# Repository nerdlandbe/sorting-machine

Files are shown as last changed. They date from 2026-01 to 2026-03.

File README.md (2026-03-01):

# M&M sorteermachine

Deze sorteermachine is met 3D-geprinte onderdelen en een aantal elektronica componenten te maken.

Het bovenste gedeelte is gebaseerd op [deze sorteermachine](https://www.instructables.com/Arduino-MM-Color-Sorter/). Het onderste gedeelte is bijgemaakt en de code is helemaal herschreven.

Met deze verbetering zie je alles nog beter en is de code ook duidelijker.

## Materiaal

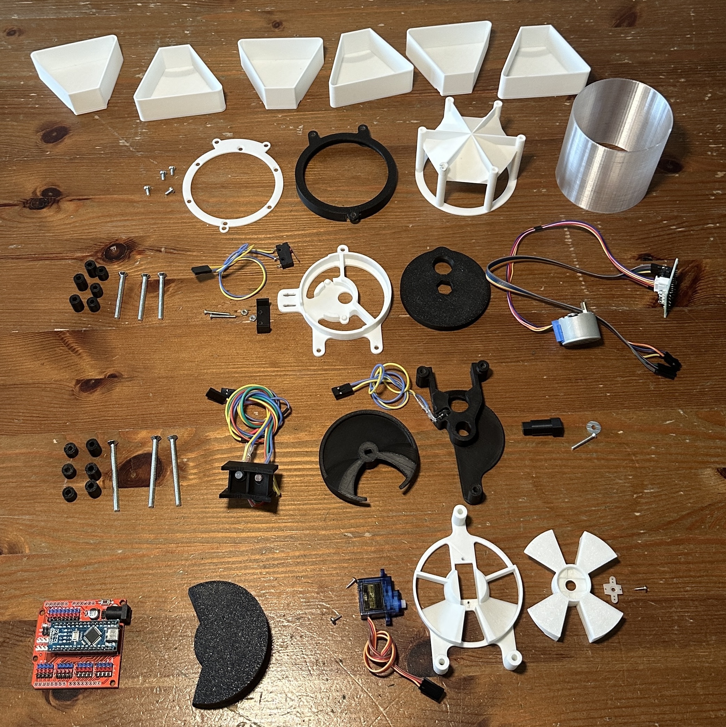
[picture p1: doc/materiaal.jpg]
Materiaal


### Te 3D-printen onderdelen

- [center_pin.stl](3D-files/center_pin.stl)
- [central_compartment.stl](3D-files/central_compartment.stl)
- [container.stl](3D-files/container.stl)
- [final_divider.stl](3D-files/final_divider.stl)
- [funnel_cap.stl](3D-files/funnel_cap.stl)
- [lid.stl](3D-files/lid.stl)
- [limit_switch_holder.stl](3D-files/limit_switch_holder.stl)
- [lower_disk.stl](3D-files/lower_disk.stl)
- [recipient.stl](3D-files/recipient.stl) (6 keer)
- [secondary_funnel.stl](3D-files/secondary_funnel.stl)
- [sensor_housing.stl](3D-files/sensor_housing.stl)
- [sorter-base.stl](3D-files/sorter-base.stl)
- [sorter-topring.stl](3D-files/sorter-topring.stl)
- [top_layer.stl](3D-files/top_layer.stl)
- [upper_disk.stl](3D-files/upper_disk.stl)
- [washer-08mm.stl](3D-files/washer-08mm.stl) (3 keer)
- [washer-10mm.stl](3D-files/washer-10mm.stl) (3 keer)
- [washer-14mm.stl](3D-files/washer-14mm.stl) (6 keer)

Je kan de kleur van alle onderdelen kiezen zoals je zelf wil, alleen [sensor_housing.stl](3D-files/sensor_housing.stl) en  [central_compartment.stl](3D-files/central_compartment.stl) moeten in het zwart om de kleurselectie te laten werken.

### Electronica componenten

- Arduino uno of nano
- Breadboard of nano expansion board
- LDR (lichtsensor)
- RGB led 5mm
- Witte led 5mm
- Weerstand 220 ohm (4 keer)
- Weerstand 10k ohm
- Microswitch [SS-5GL](https://www.amazon.com.be/s?k=micro+switch+SS-5GL)
- Servo motor [Microservo 9G + accessoires](https://www.amazon.com.be/Micro-9g-Servo/s?k=Micro+9g+Servo)
- Stepper motor [5V 28BYJ-48 met ULN2003 drivershield](https://www.amazon.com.be/s?k=stepper+28BYJ-48+ULN2003)
- Dupont breadboardkabels
- Montagekabels

### Montage

- Bout M4 X 50 (3 stuks)
- Bout M4 X 40 (3 stuks)
- Bout M3 x 5 of M3 x 8 (4 stuks)
- Bout M2.5 x 20 (3 stuks)
- Moer M2.5 (2 stuks)
- Rondel M2.5 (1 stuk)
- Vijsjes die bij de servokit zitten

### Code

Laad deze repo in Visual Studio Code, pas mogelijks [platformio.ini](platformio.ini) aan om de juiste arduino te selecteren en laad de code op.

Alle code staat in [main.cpp](src/main.cpp) mocht je de Arduino IDE gebruiken.

## Electronicaschema

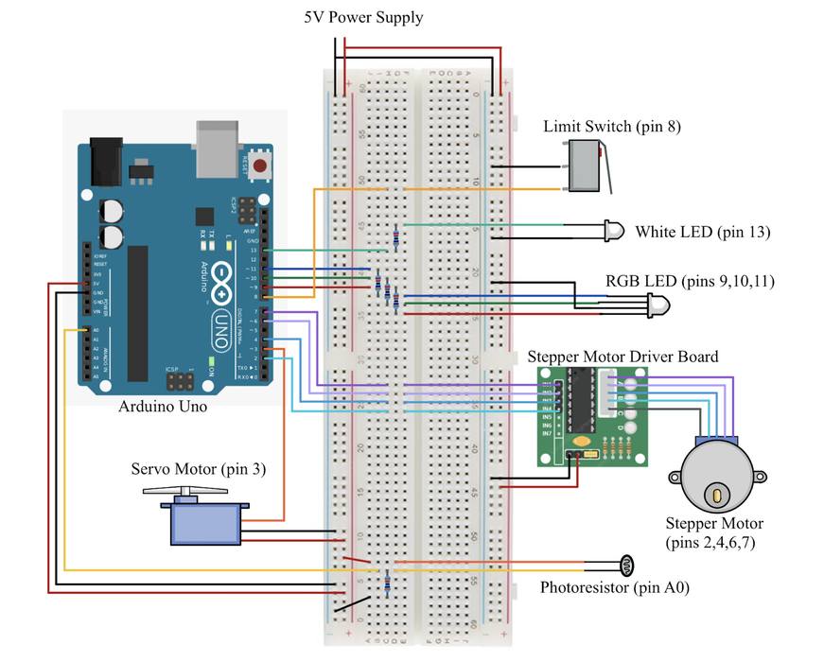
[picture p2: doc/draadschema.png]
draadschema


Ofwel gebruik je arduino (uno of nano) en een breadboard, ofwel een arduino nano met [expansion board](https://www.amazon.com.be/s?k=arduino+nano+expansion+board) (zoals bij de opnames).

## Montage bovenste gedeelte

Het bovenste gedeelte is gebaseerd op de [M&M sorter](https://www.instructables.com/Arduino-MM-Color-Sorter/) van Jackofalltrades_.

Als het onduidelijk is hoe de onderdelen tegen elkaar moeten geplaatst worden, dit is het schema van de onderdelen van het bovenste gedeelte:

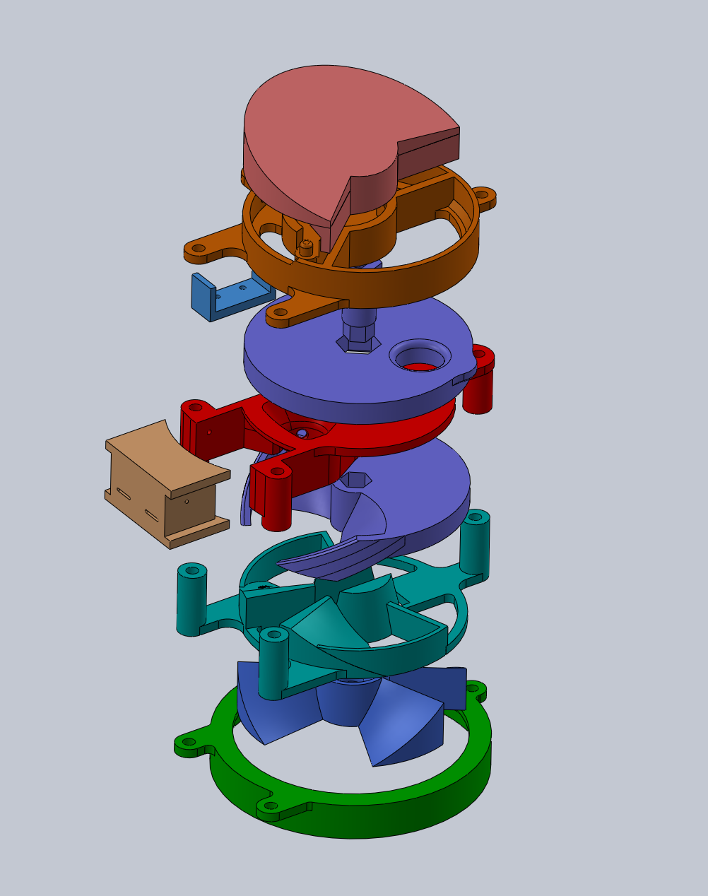
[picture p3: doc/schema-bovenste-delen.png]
bovenste delen


### Servo + behuizing onderste sorteerder

Bij de servo zitten vijsjes en ook een wit kruis dat je op de servo kan vijzen. Je moet dit een beetje bijknippen zoals op de foto's hieronder. Op die manier past het in de 3D-print.

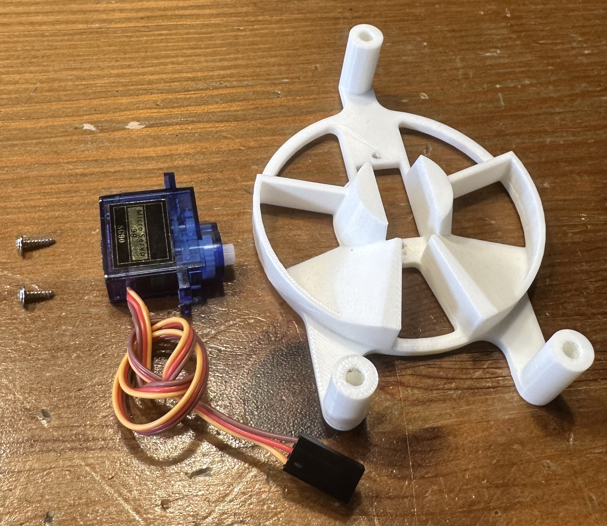
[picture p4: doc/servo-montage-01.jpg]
Servo stap 1

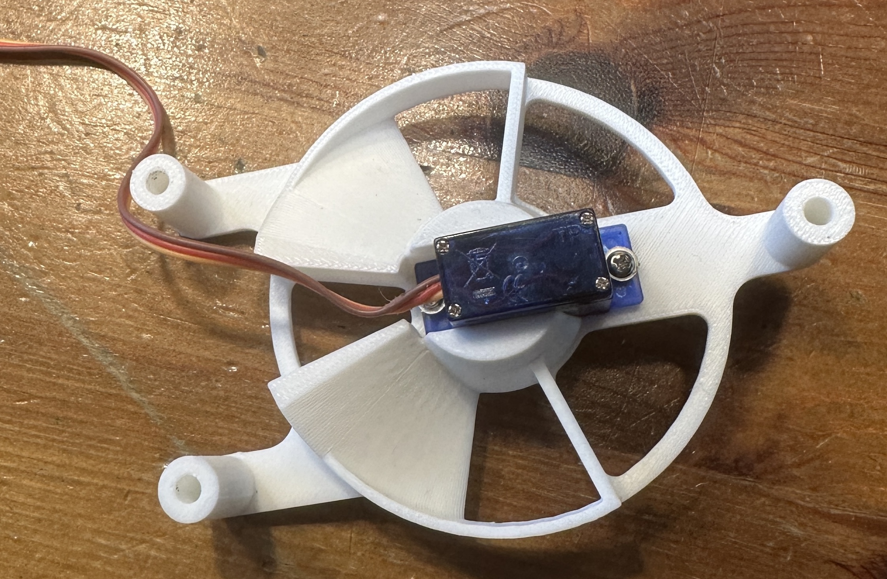
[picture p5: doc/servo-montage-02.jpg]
Servo stap 2

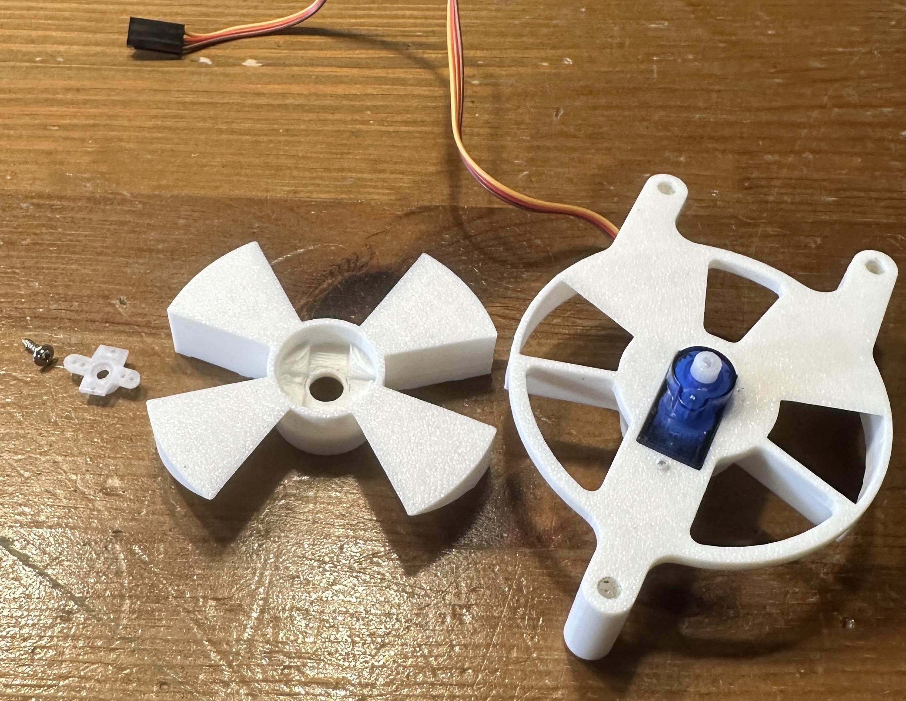
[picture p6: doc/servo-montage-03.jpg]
Servo stap 3

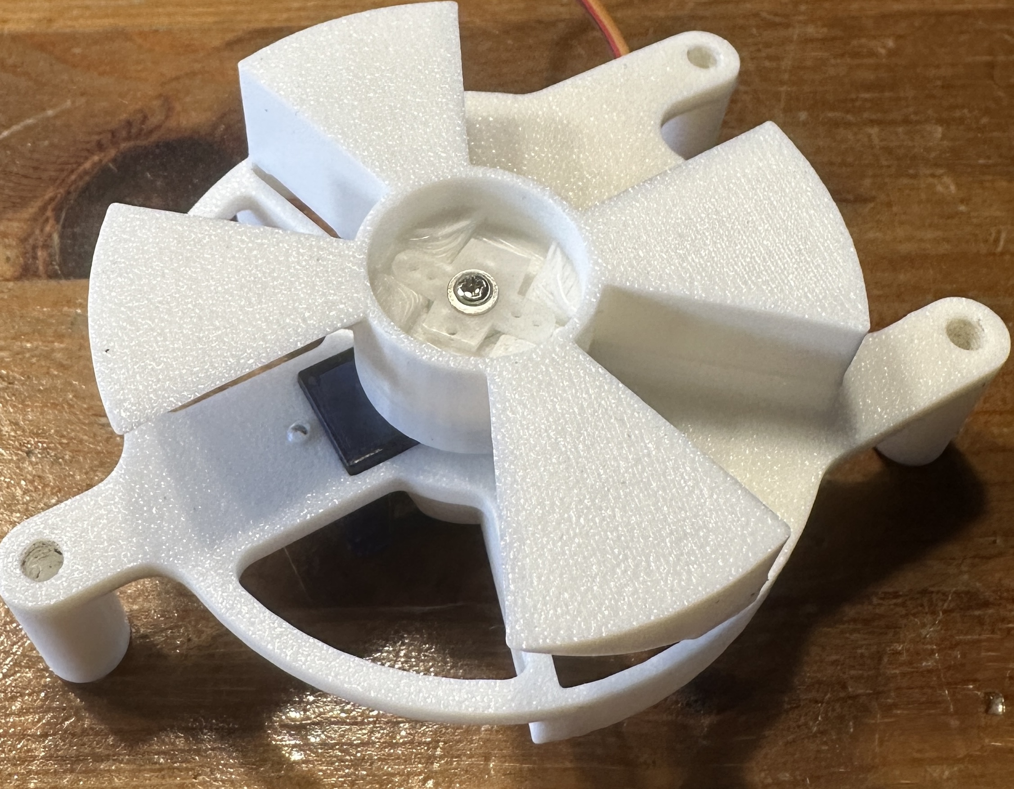
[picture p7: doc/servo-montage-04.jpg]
Servo stap 4


### Witte led behuizing

Gebruik een 220 Ohm weerstand voor de witte led.
Soldeer draadjes aan de led om de led en de weerstand te kunnen verbinden.
Lijm de led daarna vast in de 3D-print.

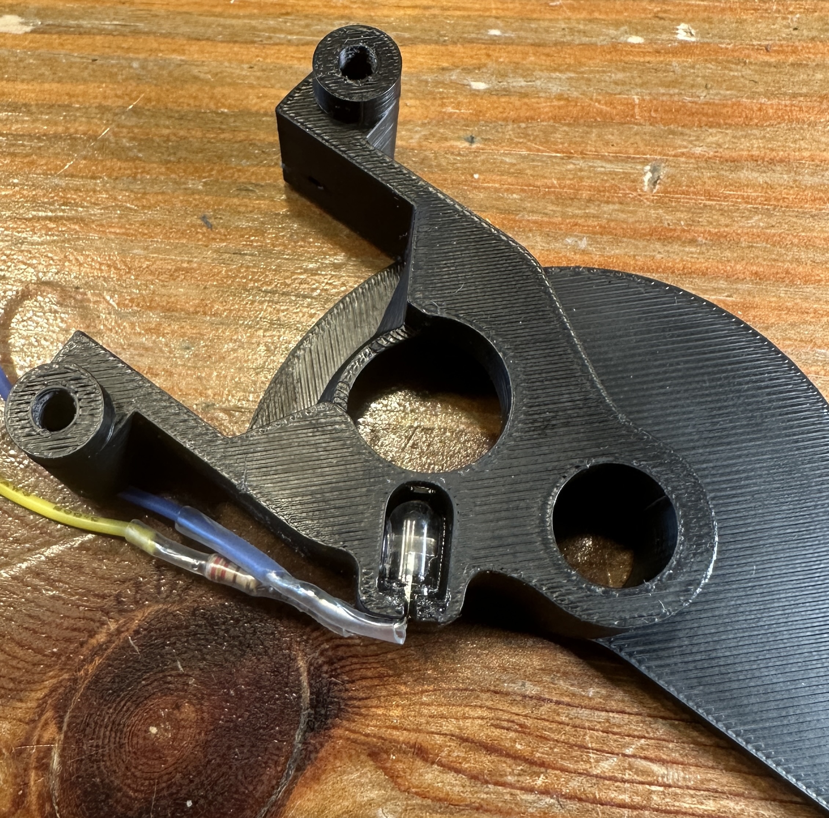
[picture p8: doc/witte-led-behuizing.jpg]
Witte led behuizing


### Bovenste sorteerder

Gebruik een M2.5 x 20 bout en rondel

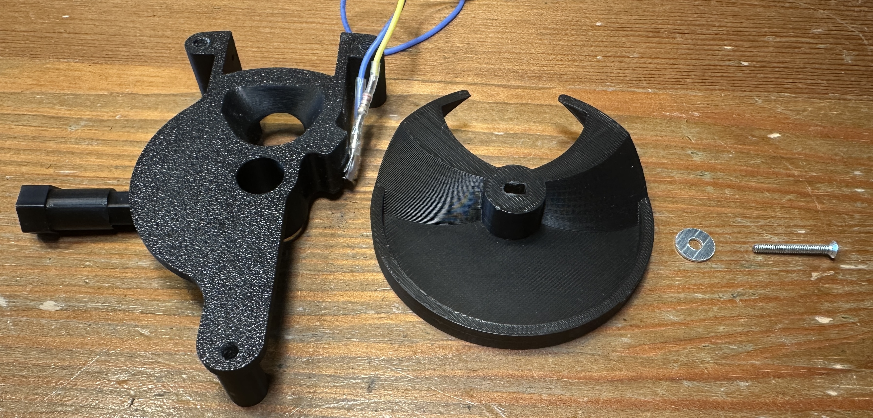
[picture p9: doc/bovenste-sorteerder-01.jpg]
bovenste sorteerder 01

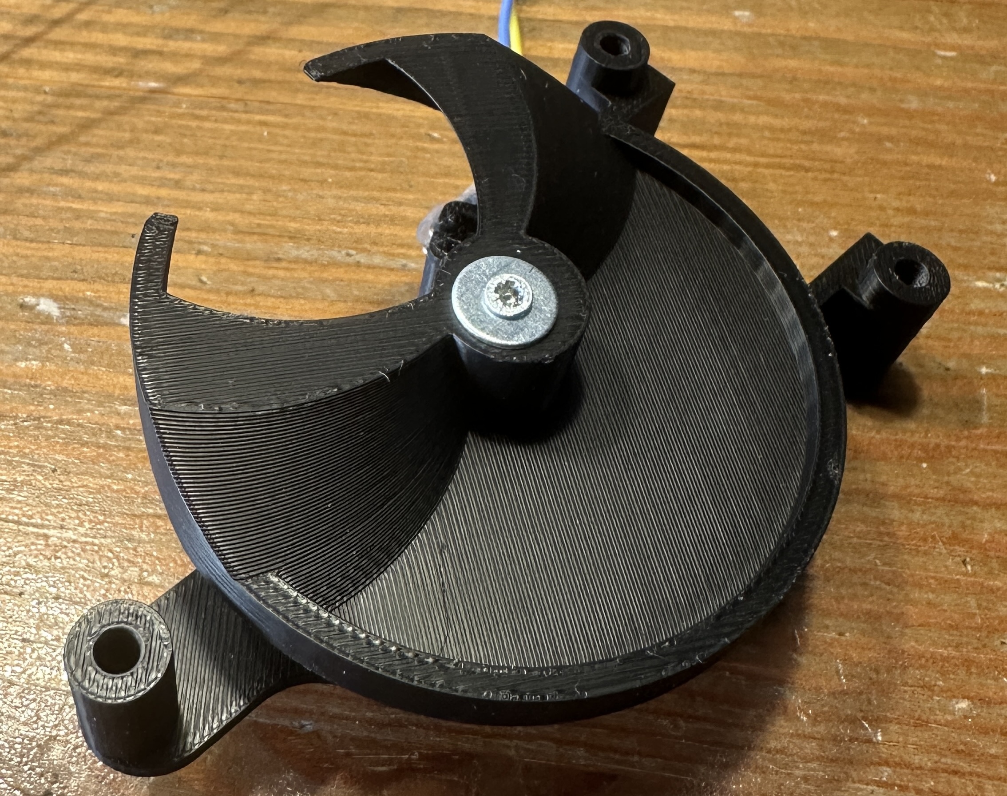
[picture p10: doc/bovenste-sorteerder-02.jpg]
bovenste sorteerder 02

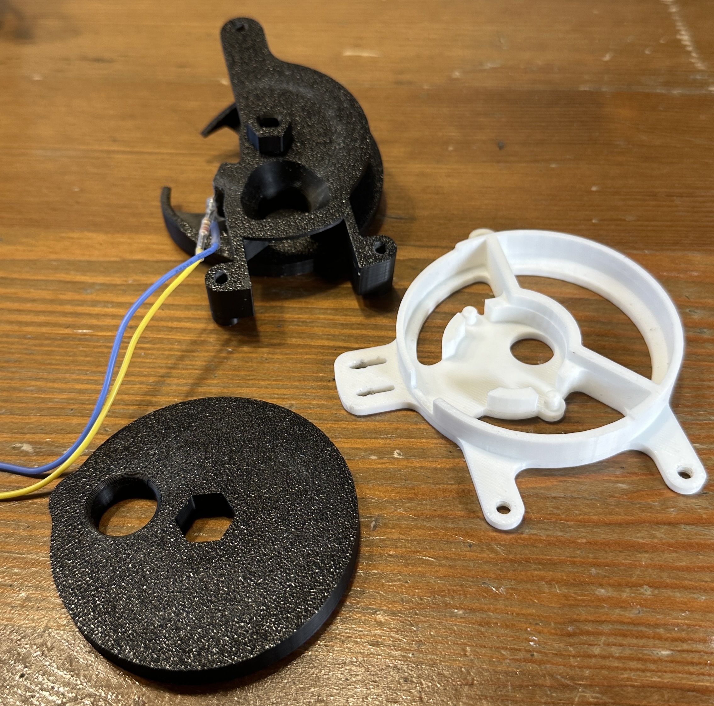
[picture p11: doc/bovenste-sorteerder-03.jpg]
bovenste sorteerder 03


### Bovenste en onderste sorteerder samen

Gebruik drie M4 X 50 bouten, drie 8mm washers en drie 14mm washers.

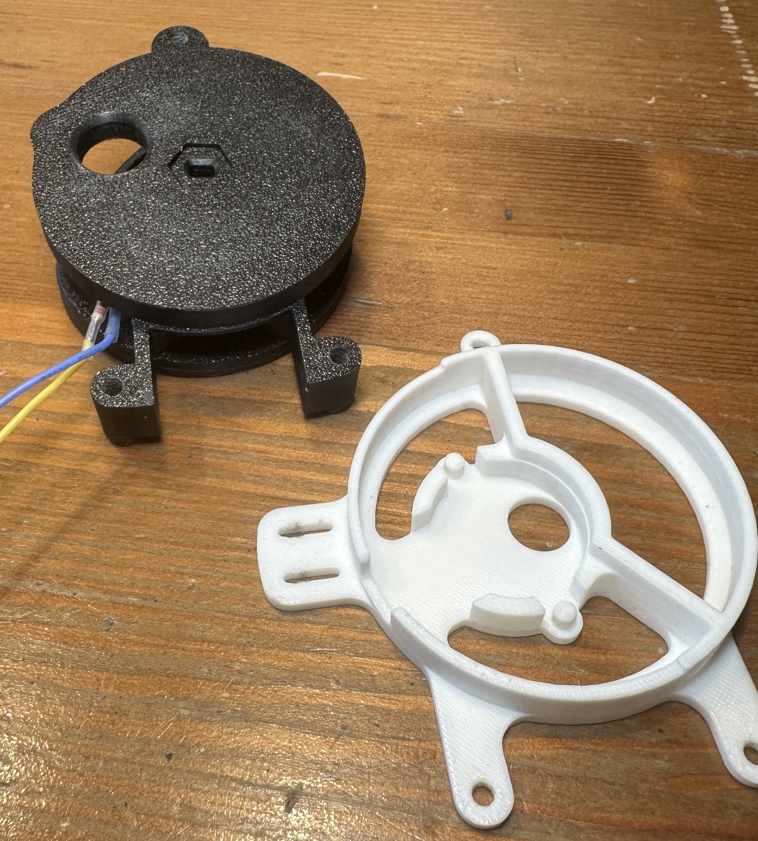
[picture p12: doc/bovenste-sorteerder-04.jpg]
bovenste sorteerder 04

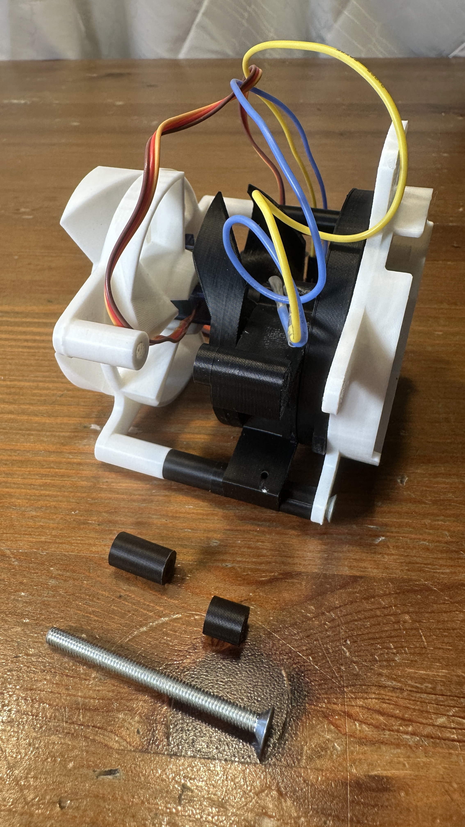
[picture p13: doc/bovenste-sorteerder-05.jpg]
bovenste sorteerder 05

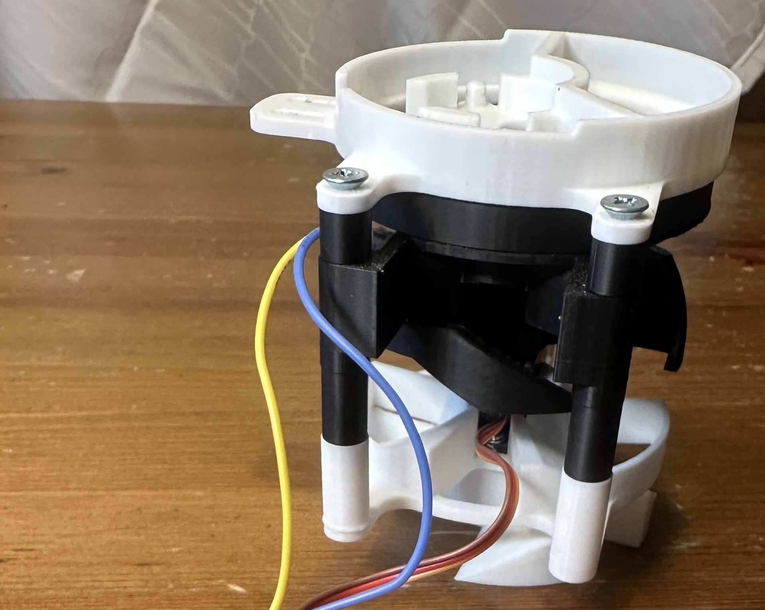
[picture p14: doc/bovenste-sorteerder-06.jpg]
Montage klaar van bovenste en onderste sorteerder


### Controlekamer

De controlekamer bestond al uit de witte LED uit een vorige stap. Met dit extra onderdeel maak je de controlekamer helemaal licht dicht.

Bevestig de RGBled (zorg dat de pin van iedere kleur een weerstand van 220 Ohm heeft) en de licht sensor (LDR sensor met zijn schakeling, zie [het draadschema](doc/draadschema.png) hiervoor).

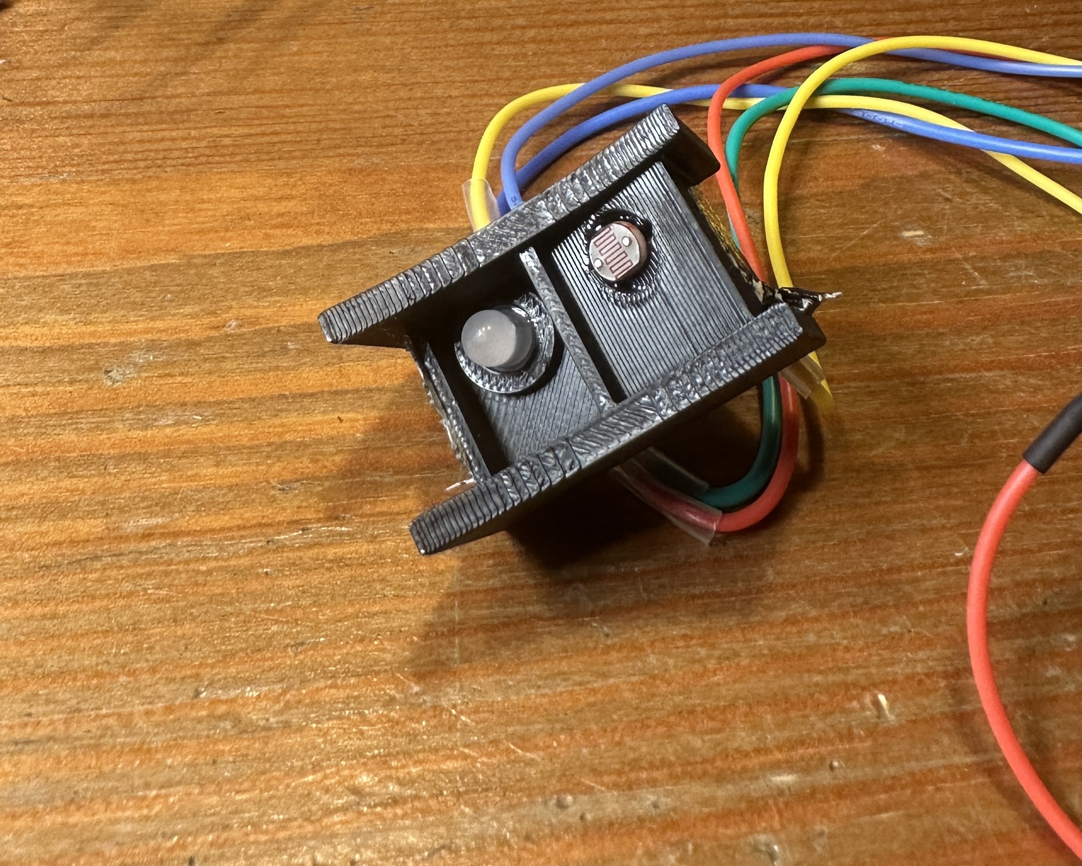
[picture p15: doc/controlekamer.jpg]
Controlekamer


Duw de gemonteerde controle zachtjes op zijn plaats. Hij moet stevig vastzitten en geen licht van buitenaf doorlaten.

Mogelijks helpt het om wat extra plakband aan te brengen zodat hij goed vast zit.

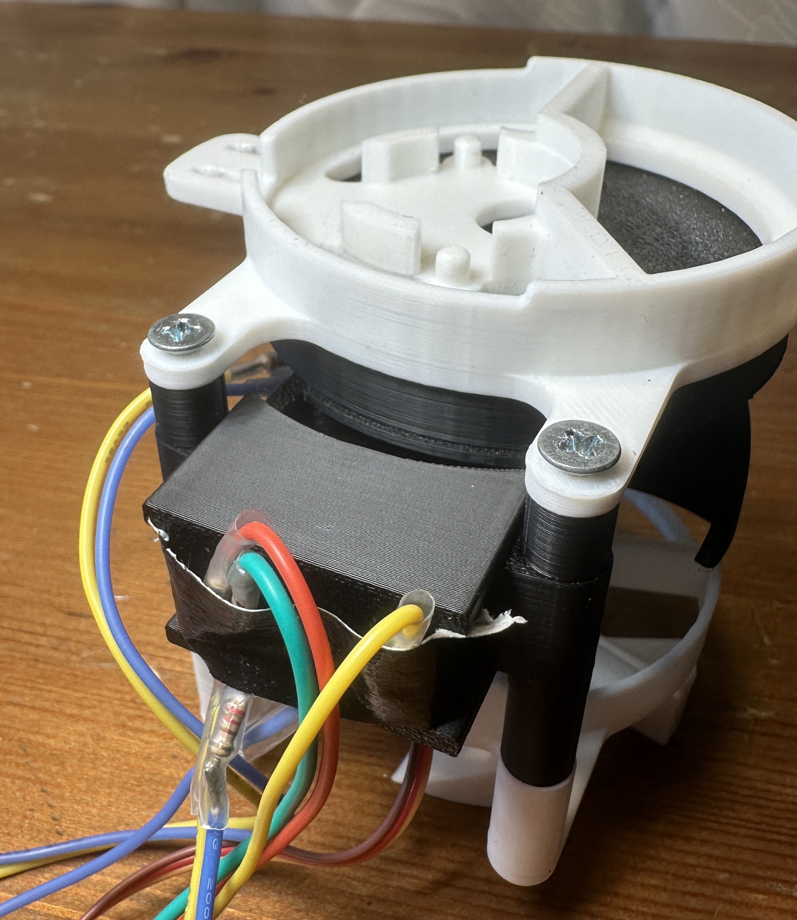
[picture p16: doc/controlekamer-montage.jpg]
montage controlekamer

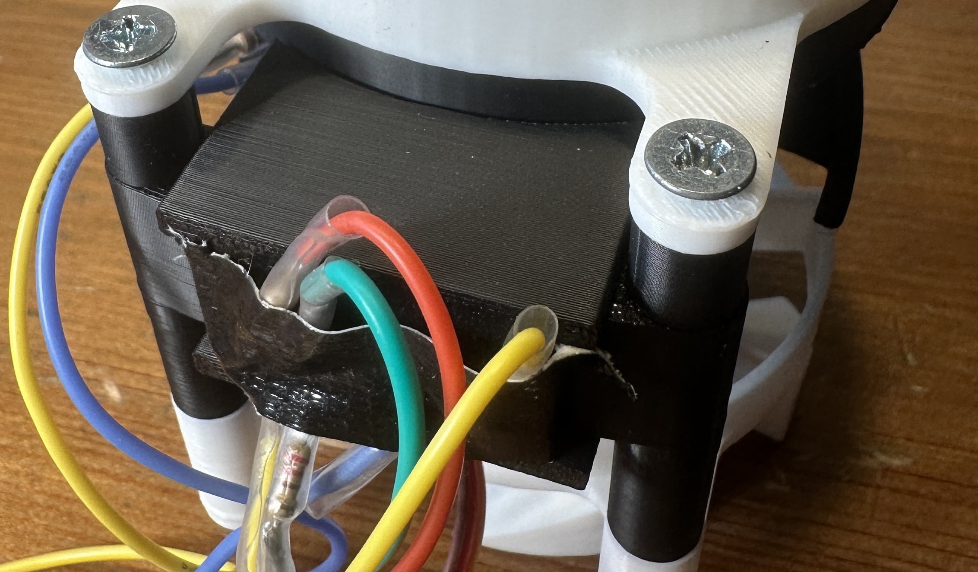
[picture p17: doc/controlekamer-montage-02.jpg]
controlekamer gemonteerd


### Microswitch

Gebruik twee M2.5 X 20 bouten en moeren.

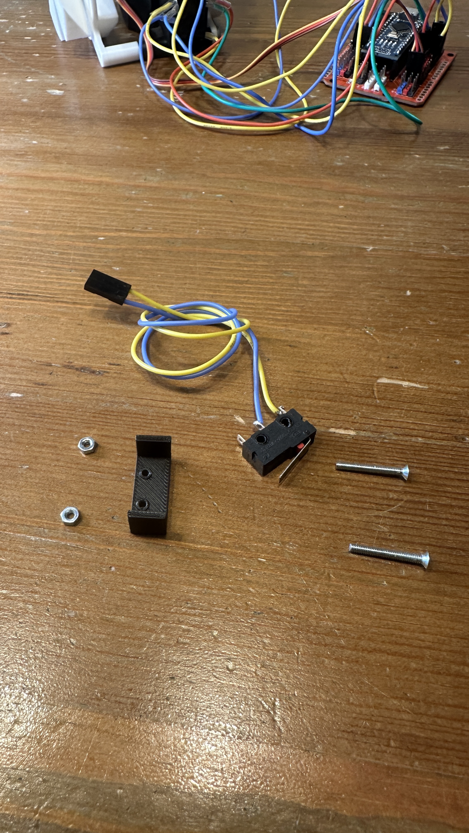
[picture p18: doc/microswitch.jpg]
Microswitch


De microswitch geeft een signaal wanneer de bovenste sorteerder een M&M in de controlekamer heeft gelegd.

Deze stap heeft wat extra mechanische configuratie nodig. De microswitch moet namelijk ingedrukt zijn (je hoort een klikje) als de verdikking van de zwarte schijf met gat voorbij de microswitch passeert.

De twee vijsjes moeten mogelijks een beetje in de gleuven van het witte onderdeel naar voor of achter geschoven worden.

Let ook op de orientatie van de microswitch. De kleuren van de draadjes op de foto kan je gebruiken om de open beugel van de microswitch in de juiste richting te monteren.

Als je de schijf een paar keer hebt kunnen ronddraaien en iedere keer een klik gehoord hebt én de schijf vlotjes is kunnen verder draaien, draai dan de vijsjes en de bouten goed vast aan.

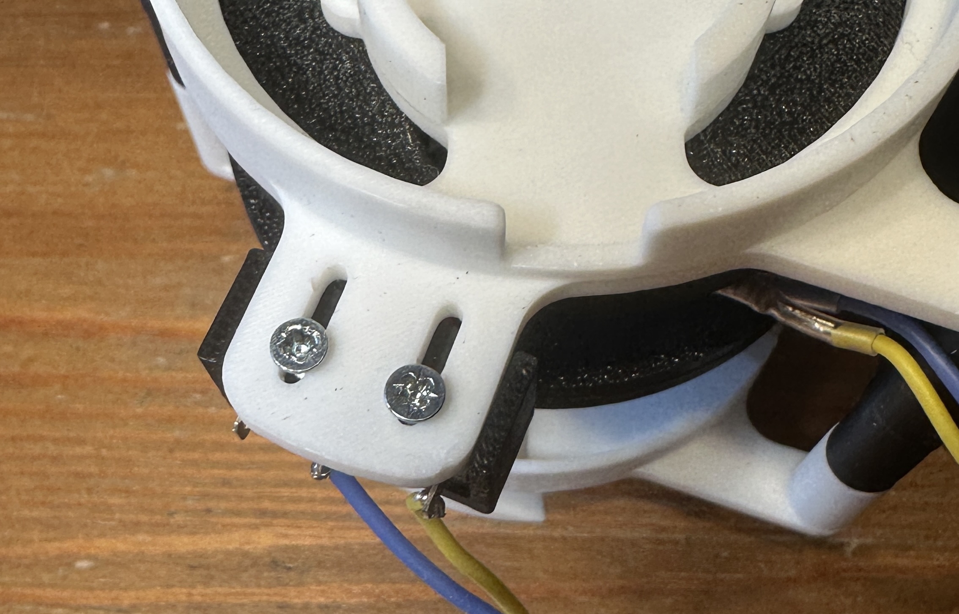
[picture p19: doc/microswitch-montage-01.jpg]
Microswitch nontage

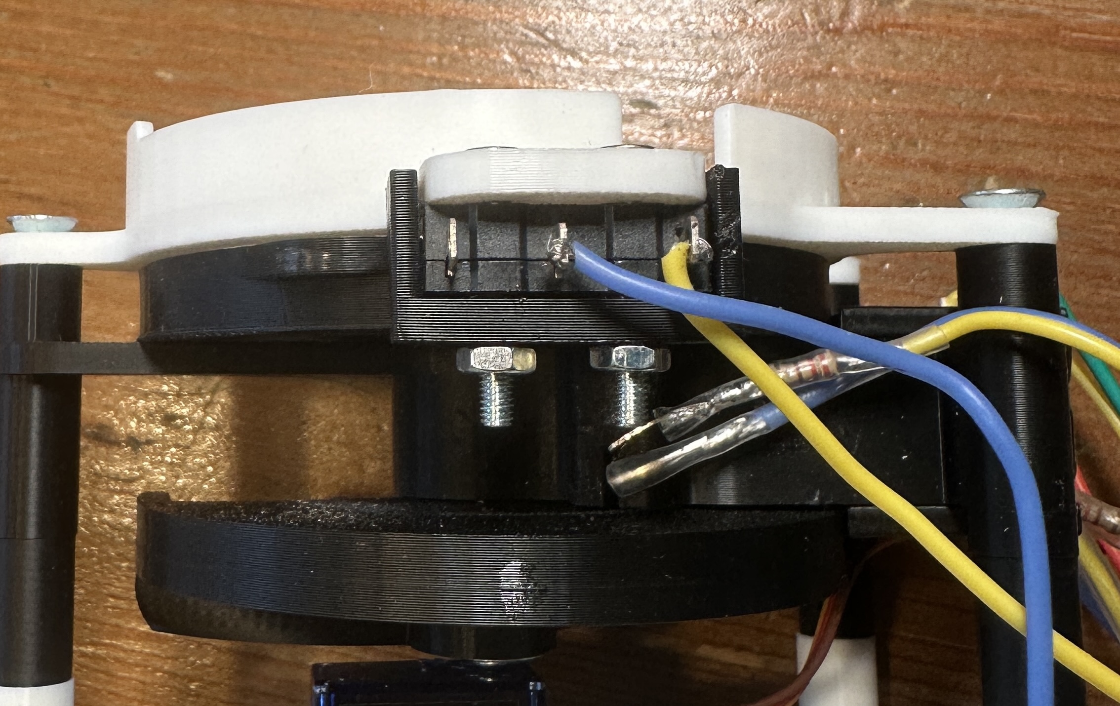
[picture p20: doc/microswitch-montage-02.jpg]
Microswitch nontage


### Steppermotor

Neem de steppermotor en je zal een rechthoekige sleuf zien. Steek de steppermotor in de witte behuizing (hij blijft normaal gezien vast zitten van zichzelf) en draai aan de zwarte schijf tot de pin van de servo mooi in de gleuf past.

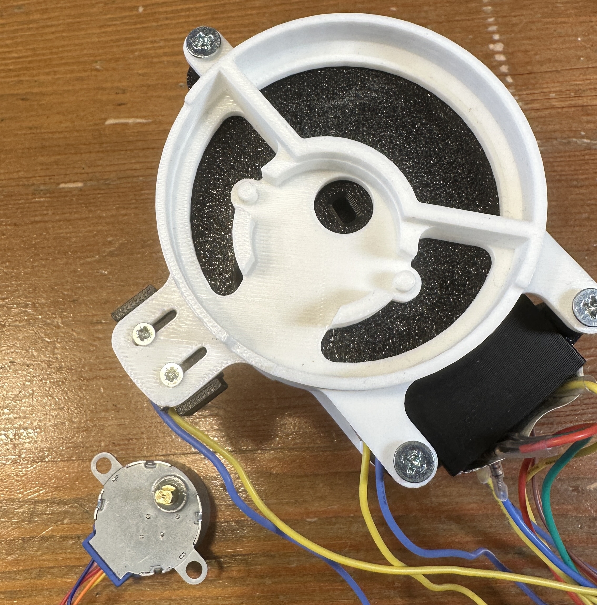
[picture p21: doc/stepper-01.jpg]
Stepper 01

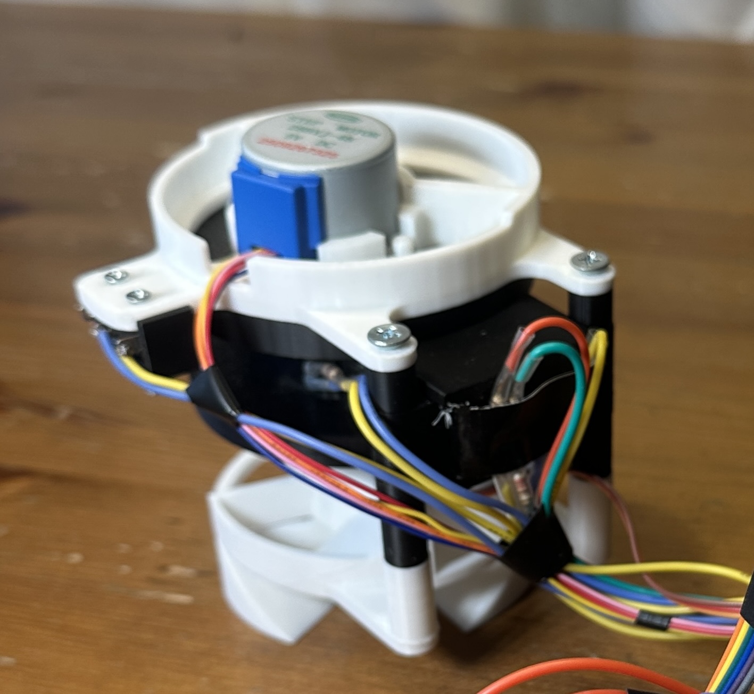
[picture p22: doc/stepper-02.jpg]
Stepper 02


### Afwerking bovenste deel

Neem wat plakband om de draadjes mooi samen te binden zodat die niet vast komen te zitten in het mechanisme.

Het bovenste deel is nu compleet!

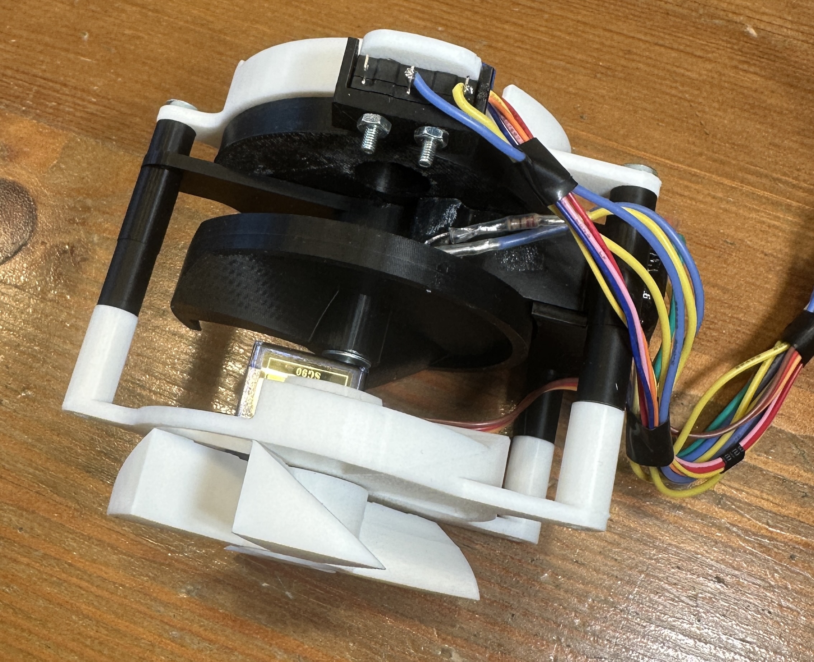
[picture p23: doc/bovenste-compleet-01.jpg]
Bovenste deel 01

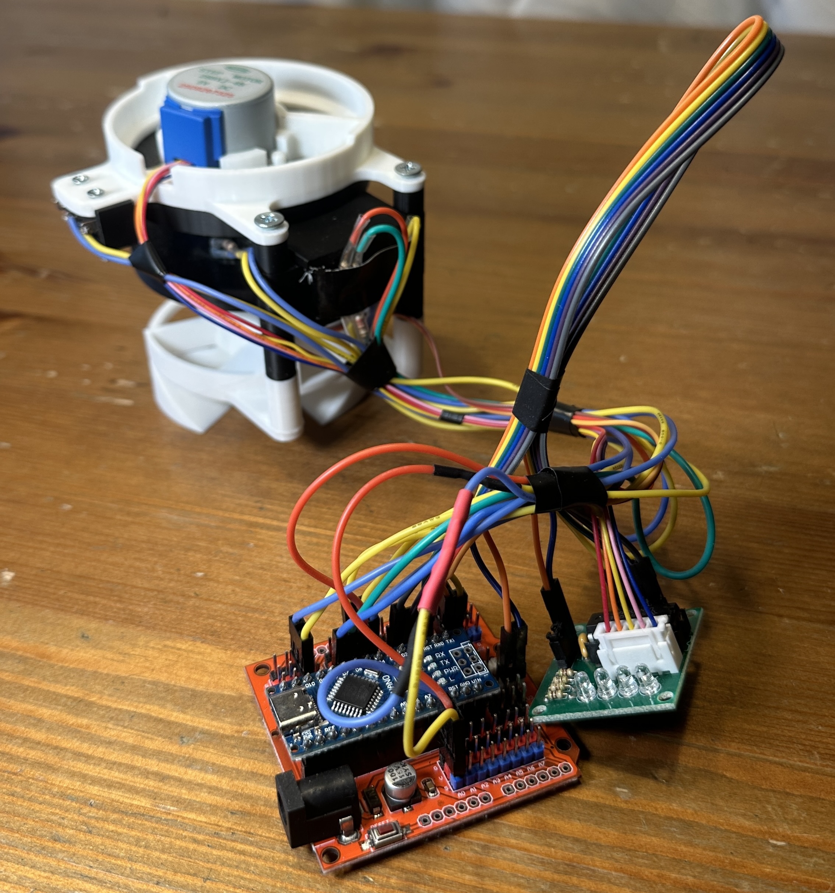
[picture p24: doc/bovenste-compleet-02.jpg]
Bovenste deel 02


## Servocalibratie

Het kan zijn dat je de onderste sorteerschijf anders gemonteerd hebt.

De onderste schijf moet op drie posities komen te staan. Om dit te testen, zoek deze lijn code en wis de twee ``//`` voor ``#define``

```
// Uncomment to do servo position testing only
//#define doServoTest true
```

Upload de code nu en de machine zal heel de tijd deze drie posities aflopen.

**Let wel op!** De machine is nog niet compleet. Hou  hem vast of zet hem ondersteboven zodat hij niet omvalt of kapot gaat. 

Kijk visueel of de posities overenkomen met de posities op de foto's hieronder.

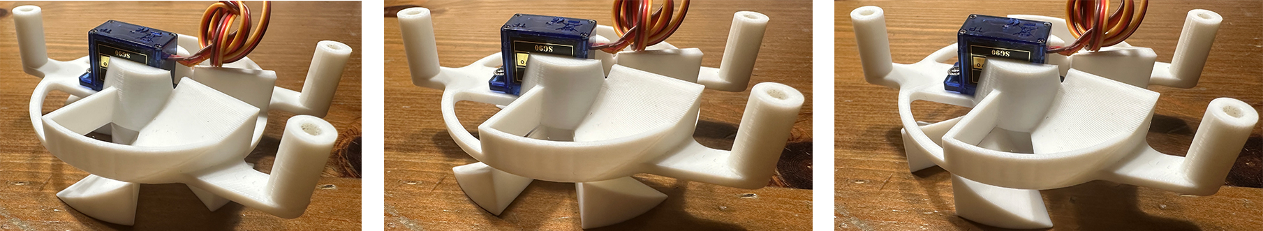
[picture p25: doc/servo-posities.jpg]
servo posities


Als dit niet zo is, heb je twee mogelijkheden: ofwel vijs je een stuk terug open, ofwel pas je de drie waardes aan in dit stuk van de code:

```
// servo positions for second stage sorting compartment
// change accrodingly to your setup
const int servoPositions[3] = {20, 55, 163};
```

Het is een beetje trial-and-error: waardes aanpassen, code uploaden, kijken wat het resultaat is, terug aanpassen en uploaden ...

Als de drie posities correct zijn, zet dan de twee ``//`` voor ``#define`` terug en upload de code nog een keer.

## Montage onderste gedeelte

Voor het onderste deel heb je de vier M3 bouten nodig, de drie M4 X 40 bouten, drie 14mm washers en drie 10mm washers.

Begin met een M4 Bout in de 3D print te steken zoals op de foto hieronder.

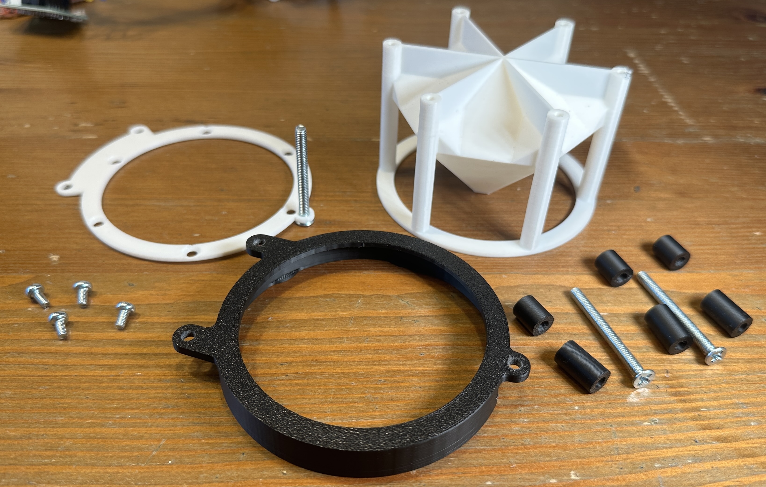
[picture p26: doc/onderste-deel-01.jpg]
Onderste deel 01


Draai daarna de vier M3 bouten in het onderste gedeelte.

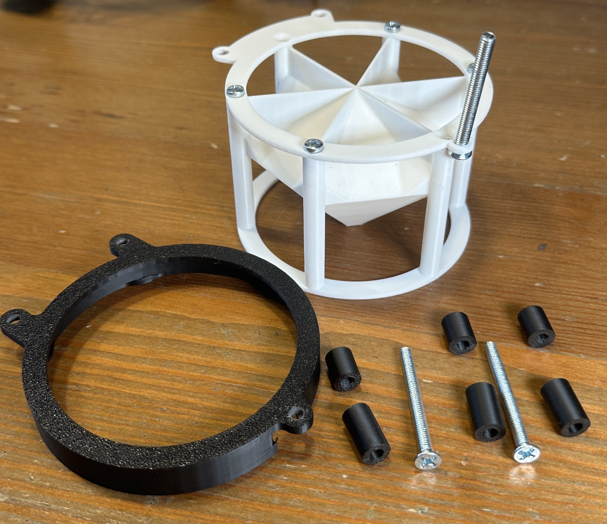
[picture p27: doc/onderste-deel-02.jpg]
Onderste deel 02


Monteer alle washers langs de drie kanten op deze manier:

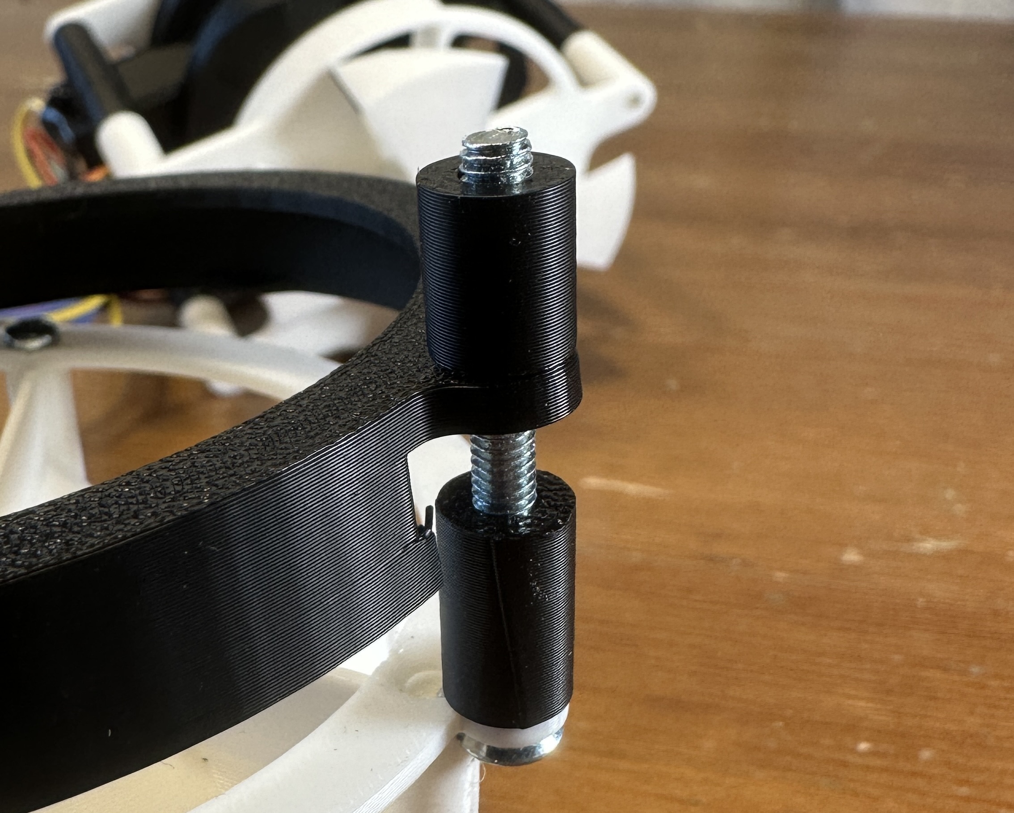
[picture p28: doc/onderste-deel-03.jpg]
Onderste deel 03


Vijs daarna het onderste gedeelte verder in het bovenste gedeelte.

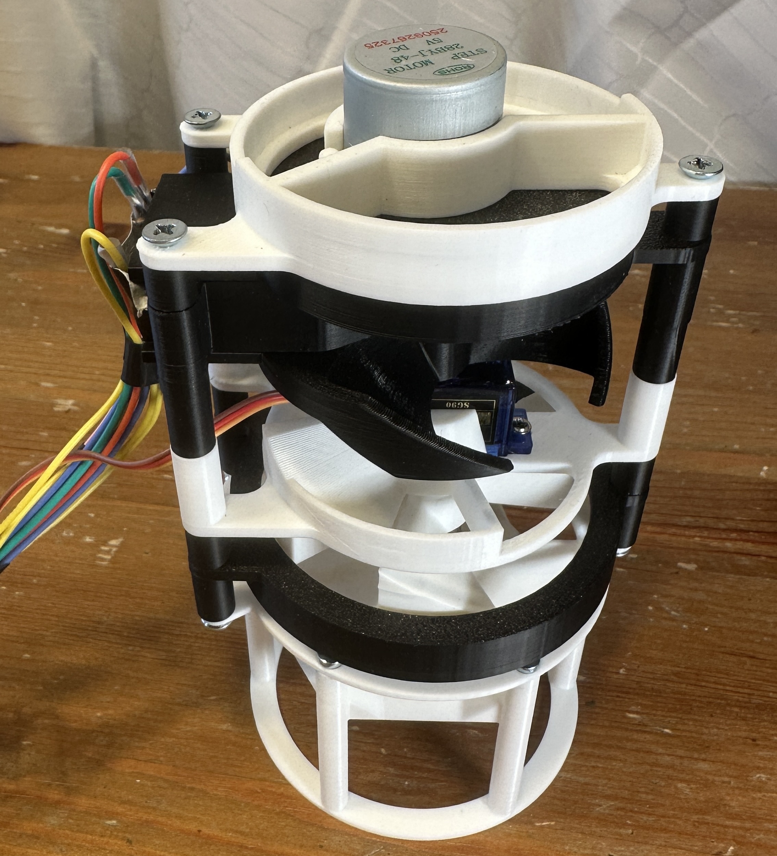
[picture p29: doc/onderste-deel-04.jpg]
Onderste deel 04


## Afwerking

Nog twee onderdelen en de machine is klaar.

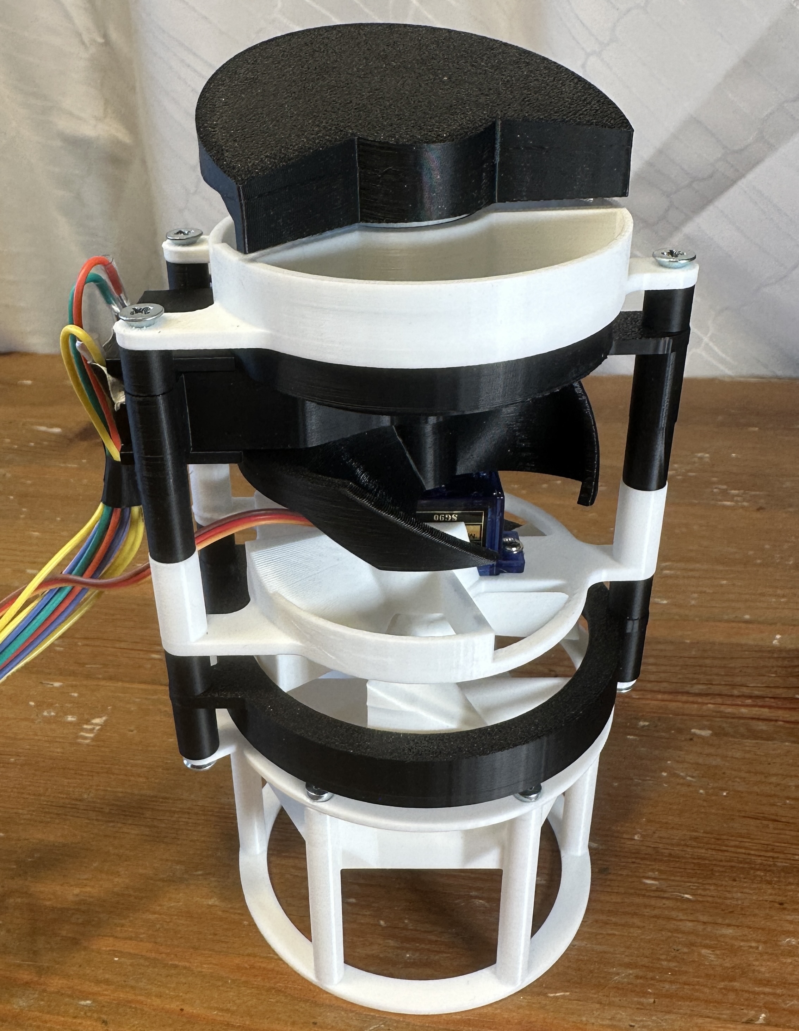
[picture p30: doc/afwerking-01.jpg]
Afwerking


De container heeft een kleine holte aan de zijkant. Deze kan je gebruiken om over de draadjes van de stepper motor te schuiven.

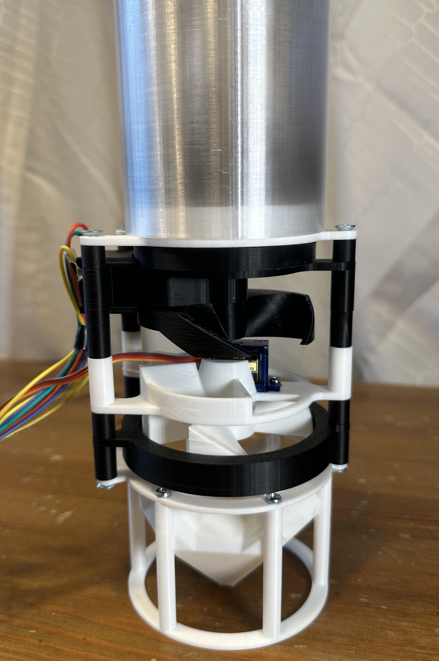
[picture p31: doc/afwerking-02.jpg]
Afwerking


Nog de zes bakjes erbij, je zal zien dat deze mooi over het randje aan de onderkant kunnen klikken.

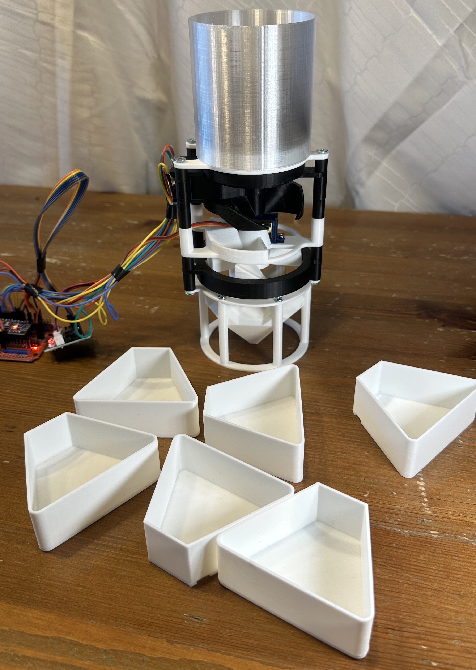
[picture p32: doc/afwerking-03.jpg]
Afwerking


## Klaar

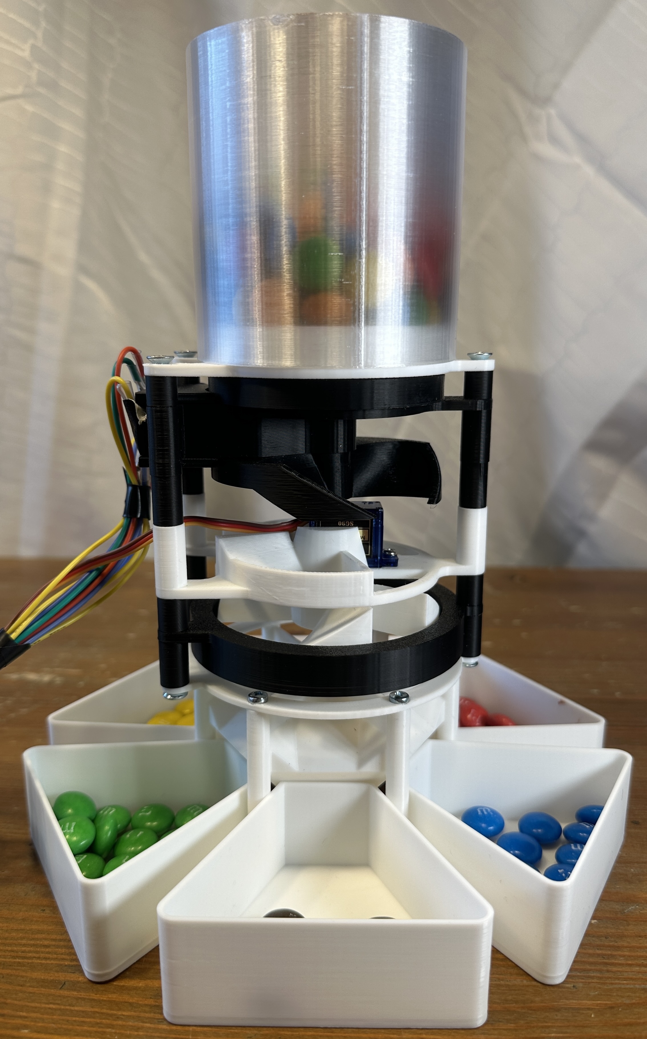
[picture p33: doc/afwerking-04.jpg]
KLaar


# Kleurcalibratie

Als de kleuren niet correct zijn, kan het zijn dat de lichtsensor of de RGB-led andere eigenschappen heeft. Dan moet je de kleurwaardes aanpassen, maar in de code zit een kalibratiefunctie ingebouwd. 

Zoek deze lijn code en wis de twee ``//`` voor ``#define``

```
// Uncomment to initialize color settings for your setup. Insert one of these m&m's in this order to set color values: red, yellow, orange, green, blue, brown
//#define doColorSetup true
```

Laad de code op en geef iedere keer een M&M van de juiste kleur.

Noteer de waardes die je ziet in de seriële monitor op je laptop. Deze waardes moet je hier in de code aanpassen:

```
ColorReference colors[colorCount] = {
    {"red", 12, 5, 5, 0},
    {"yellow", 13, 10, 5, 0},
    {"orange", 12, 7, 4, 0},
    {"green", 7, 9, 5, 0},
    {"blue", 6, 6, 6, 0},
    {"brown", 7, 5, 4, 0}};
```

Zet daarna terug twee ``//`` voor ``#define`` en upload de nieuwe code. De kleurwaardes zijn nu gecalibreerd.

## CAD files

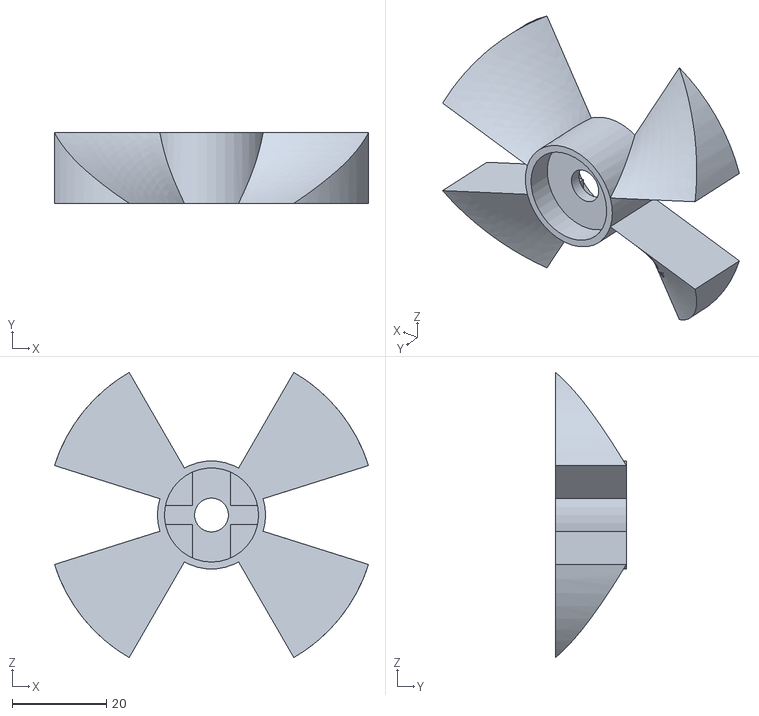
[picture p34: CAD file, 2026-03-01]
3D-files/final_divider.stl
66.8 x 15.0 x 60.6

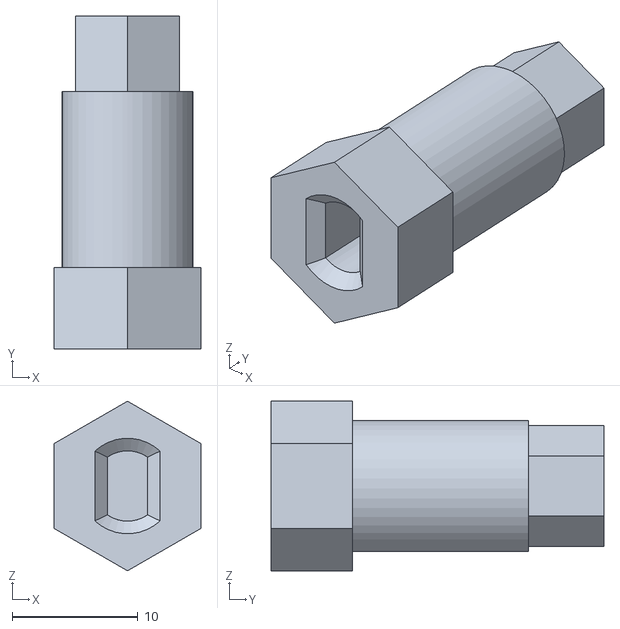
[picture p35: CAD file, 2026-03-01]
3D-files/center_pin.stl
11.7 x 26.5 x 13.5

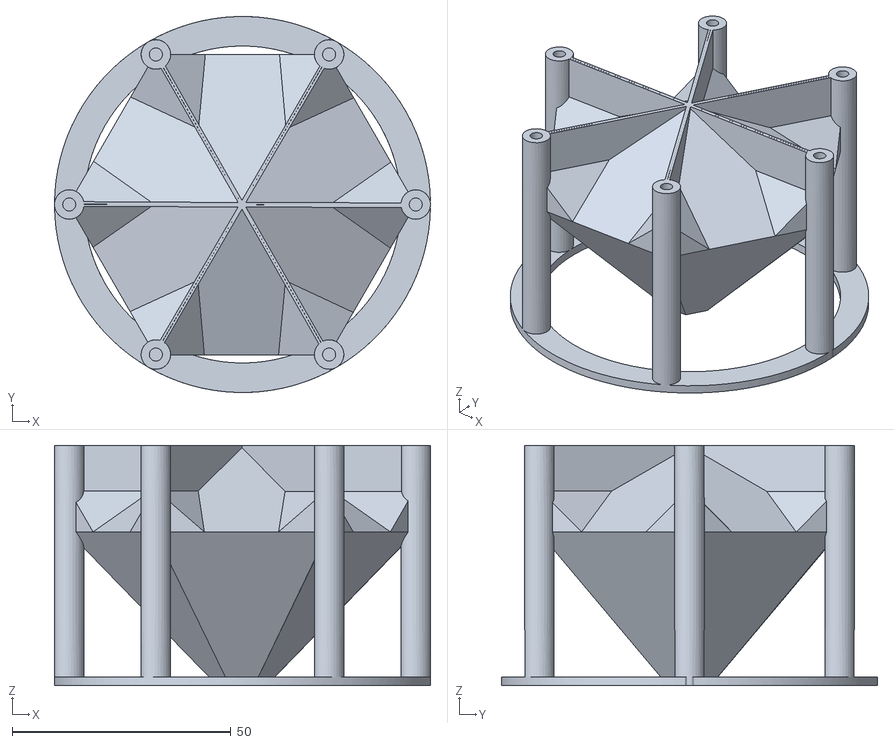
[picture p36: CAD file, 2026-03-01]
3D-files/sorter-base.stl
86.0 x 86.0 x 55.0

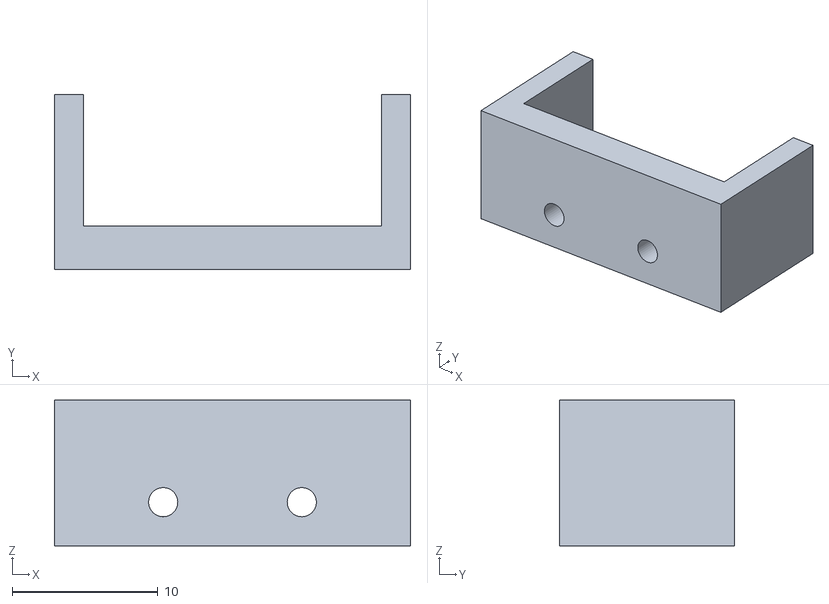
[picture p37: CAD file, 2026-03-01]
3D-files/limit_switch_holder.stl
24.4 x 12.0 x 10.0

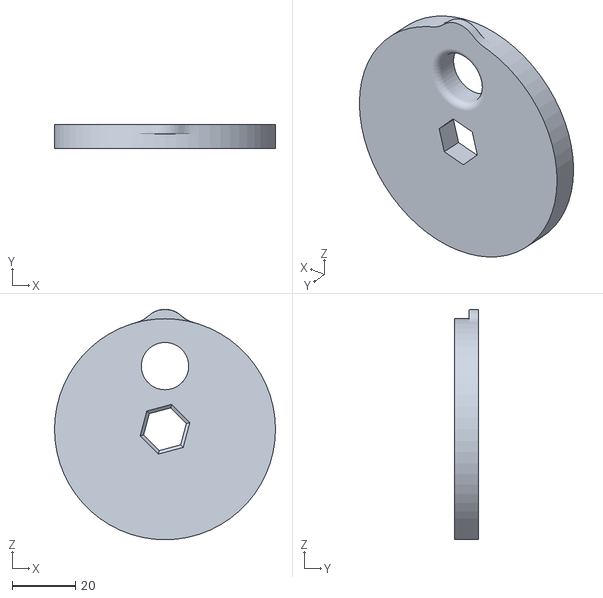
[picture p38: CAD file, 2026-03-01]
3D-files/upper_disk.stl
70.0 x 7.50 x 73.0

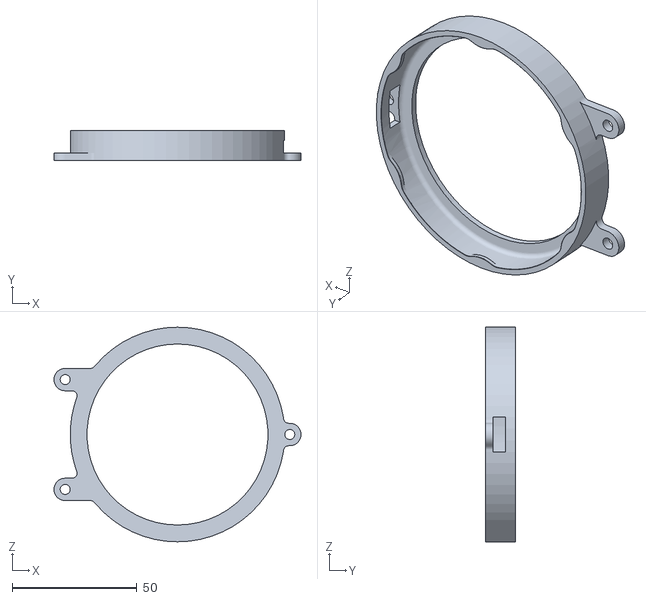
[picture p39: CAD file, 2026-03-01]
3D-files/lid.stl
99.0 x 12.0 x 86.0

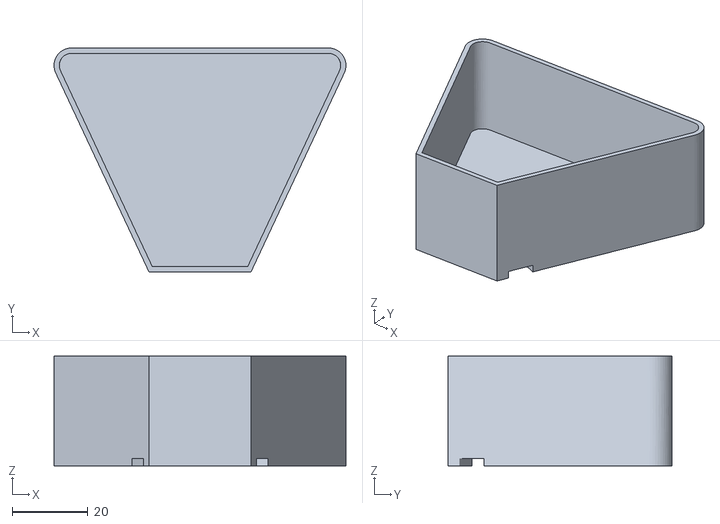
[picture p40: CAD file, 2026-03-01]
3D-files/recipient.stl
77.2 x 59.2 x 29.0

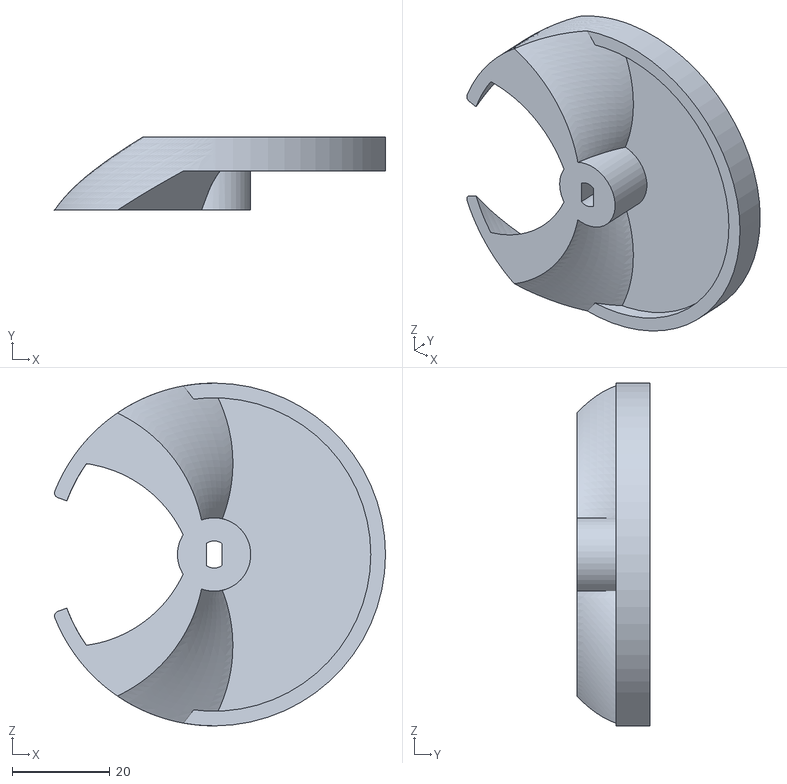
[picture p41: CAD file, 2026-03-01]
3D-files/lower_disk.stl
67.6 x 15.0 x 70.0

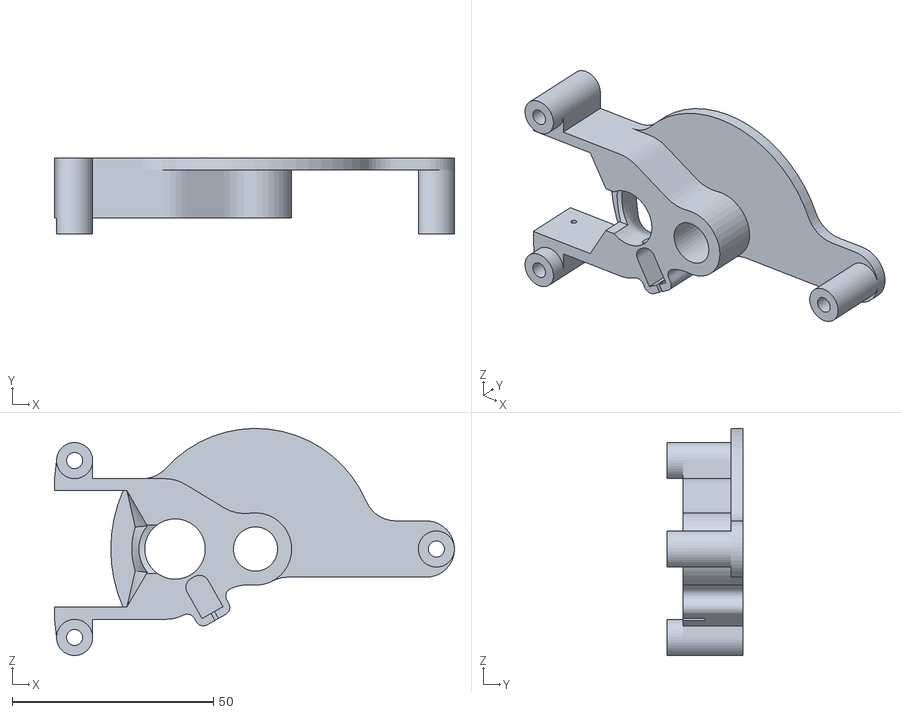
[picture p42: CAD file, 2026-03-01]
3D-files/central_compartment.stl
99.5 x 19.0 x 56.5

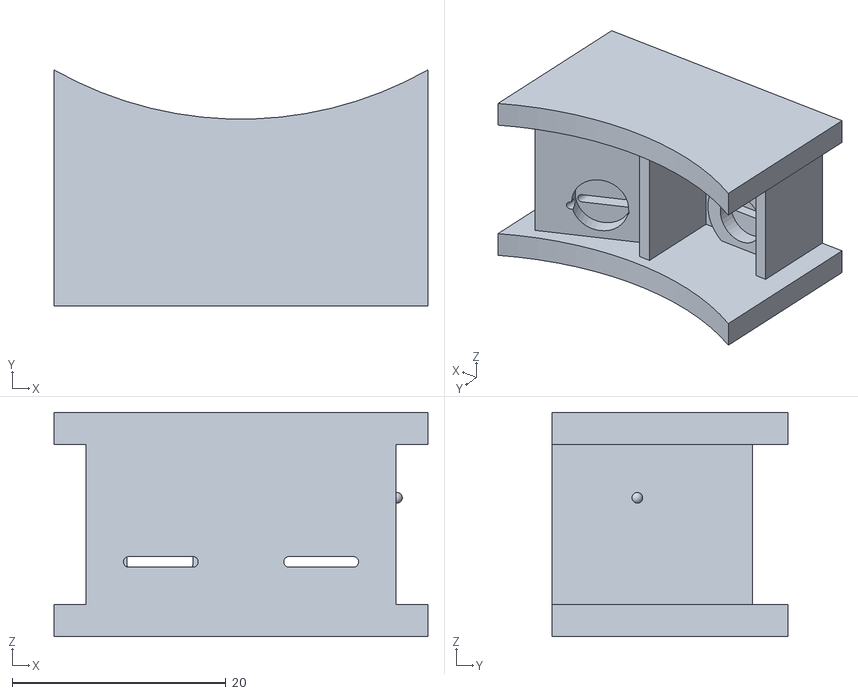
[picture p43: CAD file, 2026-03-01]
3D-files/sensor_housing.stl
35.0 x 22.1 x 21.0

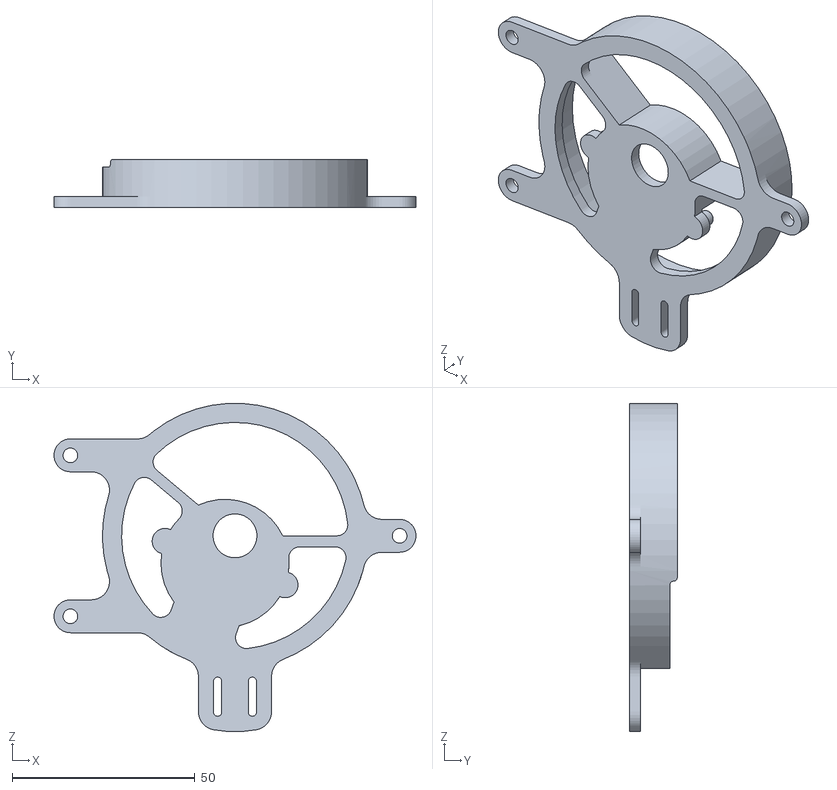
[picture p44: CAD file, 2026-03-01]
3D-files/top_layer.stl
99.0 x 13.0 x 89.7

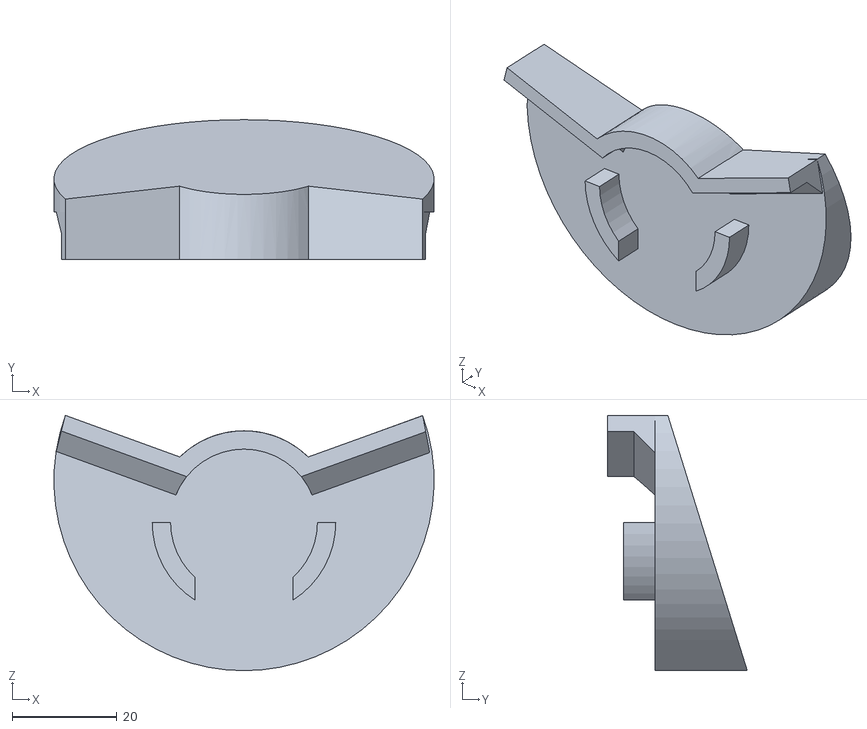
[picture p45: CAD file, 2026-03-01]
3D-files/funnel_cap.stl
72.5 x 26.6 x 48.7

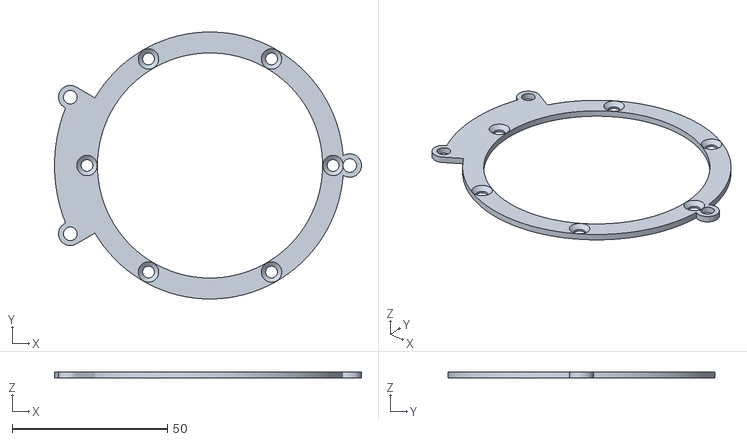
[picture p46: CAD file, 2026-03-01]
3D-files/sorter-topring.stl
98.9 x 86.0 x 2.00

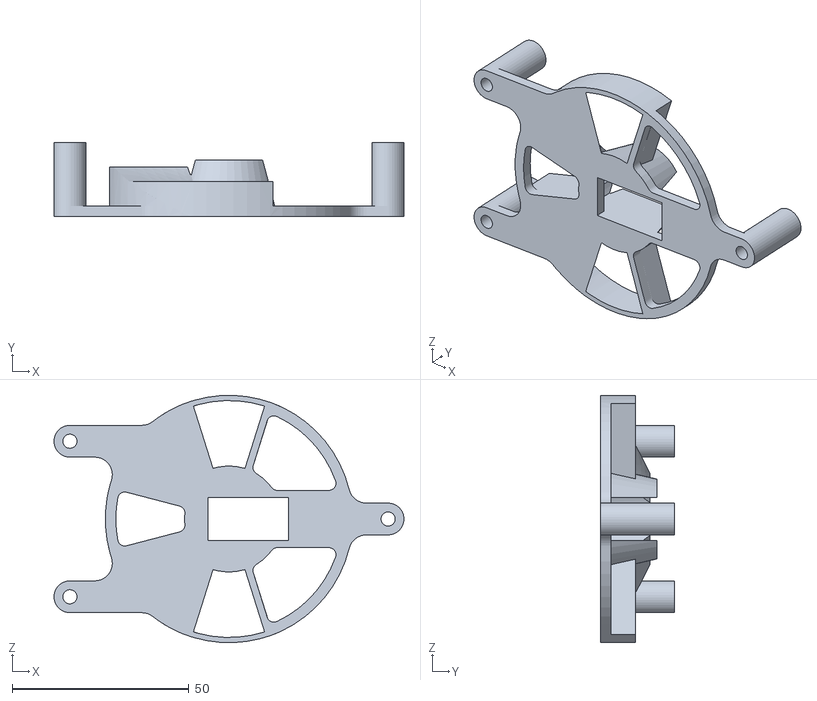
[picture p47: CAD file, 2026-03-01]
3D-files/secondary_funnel.stl
99.0 x 21.0 x 69.9

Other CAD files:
3D-files/container.stl
3D-files/washer-14mm.stl
3D-files/washer-08mm.stl
3D-files/washer-10mm.stl

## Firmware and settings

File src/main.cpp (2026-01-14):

// based on https://www.instructables.com/Arduino-MM-Color-Sorter/

#include <Arduino.h>

// Uncomment to initialize color settings for your setup. Insert one of these m&m's in this order to set color values: red, yellow, orange, green, blue, brown
//#define doColorSetup true

// Uncomment to do servo position testing only
//#define doServoTest true

// servo positions for second stage sorting compartment
// change accrodingly to your setup
const int servoPositions[3] = {20, 55, 163};

const int redPin = 9;
const int greenPin = 10;
const int bluePin = 11;
const int whitePin = 13;
const int limitPin = 8;
const int servoPin = 3;

const int lightSensorPin = A0;
const int lightThreshold = 8;
const int sampleCount = 50;  // number of samples to take for each color reading
const int stabilizationDelay = 300;  // Time for LED to stabilize before reading

struct ColorReference {
    const String name;
    int red;
    int green;
    int blue;
    int count;
};

const int colorCount = 6;

ColorReference colors[colorCount] = {
    {"red", 12, 5, 5, 0},
    {"yellow", 13, 10, 5, 0},
    {"orange", 12, 7, 4, 0},
    {"green", 7, 9, 5, 0},
    {"blue", 6, 6, 6, 0},
    {"brown", 7, 5, 4, 0}};

ColorReference testColor = {"test", 0, 0, 0, 0};

int emptyChamberCount = 0;
const int maxEmptyChamberCount = 5;

#include <Stepper.h>
Stepper myStepper = Stepper(2048, 2, 6, 4, 7);

#include <Servo.h>
Servo myServo;

/**
 * @brief Sets the color of the LED by specifying the intensity of red, green, and blue components.
 *
 * @param redValue Intensity of the red component (0-255).
 * @param greenValue Intensity of the green component (0-255).
 * @param blueValue Intensity of the blue component (0-255).
 */
void setLED(int redValue, int greenValue, int blueValue) {
    analogWrite(redPin, redValue);
    analogWrite(greenPin, greenValue);
    analogWrite(bluePin, blueValue);
}

/**
 * @brief Updates the reference color array with newly associated values.
 *
 * @param colorId The index of the color to update in the colors array.
 */
void updateColorReference(int colorId) {
    // updates the color reference array with newly associated values
    for (int i = 0; i < 3; i++) {
        colors[colorId].red = colors[colorId].red + ((testColor.red - colors[colorId].red) / (colors[colorId].count + 1));
        colors[colorId].green = colors[colorId].green + ((testColor.green - colors[colorId].green) / (colors[colorId].count + 1));
        colors[colorId].blue = colors[colorId].blue + ((testColor.blue - colors[colorId].blue) / (colors[colorId].count + 1));
    }
    // incriments the color array counter (how many of this color have been sorted)
    colors[colorId].count++;
}

/**
 * @brief Moves the stepper motor clockwise until the limit switch is triggered.
 *
 */
void moveToLimit() {
    int i = 0;  // provides failsafe for jamming
    myStepper.step(200);
    while (digitalRead(limitPin) == HIGH) {
        myStepper.step(10);
        if (i > 200) {
            Serial.println("Jammed, Reversing");
            myStepper.step(-300);
            i = 0;
        }
        i++;
    }
    Serial.println("Limit Reached");
}

/**
 * @brief Tests the color by reading the light sensor values under different LED colors.
 * Stores the averaged RGB values in testColor.
 *
 */
void getColorValues() {
    // check if chamber is not empty
    digitalWrite(whitePin, HIGH);
    delay(100);  // Increased delay for white LED stabilization
    int check = analogRead(lightSensorPin);
    digitalWrite(whitePin, LOW);

    Serial.print("Light Check: ");
    Serial.println(check);

    // if the chamber is empty, return zeros
    if (check >= lightThreshold) {
        Serial.println("Nothing in chamber");
        emptyChamberCount++;
        testColor.red = 0;
        testColor.green = 0;
        testColor.blue = 0;
        return;
    }

    delay(100);
    emptyChamberCount = 0;

    Serial.println("Testing Color...");

    // Measure ambient light level (LED off)
    setLED(0, 0, 0);
    delay(50);
    int ambient = 0;
    for (int i = 0; i < 10; i++) {
        ambient += analogRead(lightSensorPin);
        delay(5);
    }
    ambient = ambient / 10;
    Serial.print("Ambient light: ");
    Serial.println(ambient);

    // Collect RED light reflection
    setLED(255, 0, 0);
    delay(stabilizationDelay);
    int readings[sampleCount];
    
    for (int i = 0; i < sampleCount; i++) {
        readings[i] = analogRead(lightSensorPin);
        delay(10);  // Small delay between readings
    }
    
    // Sort and take median to filter outliers
    for (int i = 0; i < sampleCount - 1; i++) {
        for (int j = 0; j < sampleCount - i - 1; j++) {
            if (readings[j] > readings[j + 1]) {
                int temp = readings[j];
                readings[j] = readings[j + 1];
                readings[j + 1] = temp;
            }
        }
    }
    
    // Average the middle 70% of readings (discard outliers)
    int startIdx = sampleCount * 0.15;
    int endIdx = sampleCount * 0.85;
    long sum = 0;
    for (int i = startIdx; i < endIdx; i++) {
        sum += readings[i];
    }
    testColor.red = sum / (endIdx - startIdx);
    
    Serial.print("Red - Min: ");
    Serial.print(readings[0]);
    Serial.print(" | Max: ");
    Serial.print(readings[sampleCount - 1]);
    Serial.print(" | Avg: ");
    Serial.print(testColor.red);
    Serial.print(" | Corrected: ");
    int correctedRed = testColor.red - ambient;
    Serial.println(correctedRed > 0 ? correctedRed : 0);

    // Collect GREEN light reflection
    setLED(0, 255, 0);
    delay(stabilizationDelay);
    
    for (int i = 0; i < sampleCount; i++) {
        readings[i] = analogRead(lightSensorPin);
        delay(10);
    }
    
    // Sort for median filtering
    for (int i = 0; i < sampleCount - 1; i++) {
        for (int j = 0; j < sampleCount - i - 1; j++) {
            if (readings[j] > readings[j + 1]) {
                int temp = readings[j];
                readings[j] = readings[j + 1];
                readings[j + 1] = temp;
            }
        }
    }
    
    sum = 0;
    for (int i = startIdx; i < endIdx; i++) {
        sum += readings[i];
    }
    testColor.green = sum / (endIdx - startIdx);
    
    Serial.print("Green - Min: ");
    Serial.print(readings[0]);
    Serial.print(" | Max: ");
    Serial.print(readings[sampleCount - 1]);
    Serial.print(" | Avg: ");
    Serial.print(testColor.green);
    Serial.print(" | Corrected: ");
    int correctedGreen = testColor.green - ambient;
    Serial.println(correctedGreen > 0 ? correctedGreen : 0);

    // Collect BLUE light reflection
    setLED(0, 0, 255);
    delay(stabilizationDelay);
    
    for (int i = 0; i < sampleCount; i++) {
        readings[i] = analogRead(lightSensorPin);
        delay(10);
    }
    
    // Sort for median filtering
    for (int i = 0; i < sampleCount - 1; i++) {
        for (int j = 0; j < sampleCount - i - 1; j++) {
            if (readings[j] > readings[j + 1]) {
                int temp = readings[j];
                readings[j] = readings[j + 1];
                readings[j + 1] = temp;
            }
        }
    }
    
    sum = 0;
    for (int i = startIdx; i < endIdx; i++) {
        sum += readings[i];
    }
    testColor.blue = sum / (endIdx - startIdx);
    
    Serial.print("Blue - Min: ");
    Serial.print(readings[0]);
    Serial.print(" | Max: ");
    Serial.print(readings[sampleCount - 1]);
    Serial.print(" | Avg: ");
    Serial.print(testColor.blue);
    Serial.print(" | Corrected: ");
    int correctedBlue = testColor.blue - ambient;
    Serial.println(correctedBlue > 0 ? correctedBlue : 0);

    // Print ratio information for color discrimination
    Serial.println("--- Color Ratios ---");
    if (testColor.green > 0) {
        Serial.print("R/G ratio: ");
        Serial.println((float)testColor.red / testColor.green);
    }
    if (testColor.blue > 0) {
        Serial.print("R/B ratio: ");
        Serial.println((float)testColor.red / testColor.blue);
        Serial.print("G/B ratio: ");
        Serial.println((float)testColor.green / testColor.blue);
    }

    // turn LED off and update overall m&m counter
    setLED(0, 0, 0);
    testColor.count++;
}

/**
 * @brief Finds the closest matching color ID based on the tested color values.
 *
 * @return int The ID of the matched color, or -1 if no match is found.
 */
int findMatch() {
    int matchedColorId = -1;

    // if chamber is empty return -1
    if (testColor.red == 0) {
        return matchedColorId;
    }

    long sums[colorCount];

    for (int i = 0; i < colorCount; i++) {
        sums[i] = pow(testColor.red - colors[i].red, 2) + pow(testColor.green - colors[i].green, 2) + pow(testColor.blue - colors[i].blue, 2);
    }

    long closest = min(sums[0], min(sums[1], min(sums[2], min(sums[3], min(sums[4], sums[5])))));

    if (closest == sums[0]) {
        matchedColorId = 0;
    } else if (closest == sums[1]) {
        matchedColorId = 1;
    } else if (closest == sums[2]) {
        matchedColorId = 2;
    } else if (closest == sums[3]) {
        matchedColorId = 3;
    } else if (closest == sums[4]) {
        matchedColorId = 4;
    } else {
        matchedColorId = 5;
    }

    colors[matchedColorId].count++;

    Serial.print("Matched Color: ");
    Serial.println(colors[matchedColorId].name);

    return matchedColorId;
}

/**
 * @brief Moves the stepper motor and servo to sort the item based on the color ID.
 *
 * @param colorId The index of the color to sort.
 */
void sort(int colorId) {
    Serial.print("Sorting to: ");
    Serial.println(colors[colorId].name);

    switch (colorId) {
        case 0:
            myServo.write(servoPositions[2]);
            myStepper.step(-1650);
            moveToLimit();
            break;
        case 1:
            myServo.write(servoPositions[1]);
            myStepper.step(-1650);
            moveToLimit();
            break;
        case 2:
            myServo.write(servoPositions[0]);
            myStepper.step(-1650);
            moveToLimit();
            break;
        case 3:
            myServo.write(servoPositions[2]);
            moveToLimit();
            break;
        case 4:
            myServo.write(servoPositions[1]);
            moveToLimit();
            break;
        case 5:
            myServo.write(servoPositions[0]);
            moveToLimit();
            break;
        default:
            Serial.println("No valid color selected for sorting");
            moveToLimit();
            break;
    }
}

/**
 * @brief Displays the sorting statistics on the serial monitor.
 *
 */
void showStats() {
    Serial.println("Sorting Complete!");
    Serial.print("Total: ");
    Serial.println(testColor.count);

    for (int i = 0; i < colorCount; i++) {
        Serial.print(colors[i].name);
        Serial.print(": ");
        Serial.println(colors[i].count);
    }

    // ends program
    delay(400);
    exit(0);
}

/**
 * @brief Set the Color References for each m&m color
 *
 */
void setColorReferences() {
    moveToLimit();

    for (int i = 0; i < colorCount; i++) {
        getColorValues();
        updateColorReference(i);
        sort(i);
    }
}

/**
 * @brief Tests the servo by moving it through predefined positions.
 *
 */
void servoTest() {
    Serial.println("Testing Servo...");

    for (int i = 0; i < 3; i++) {
        Serial.print("Position ");
        Serial.println(i);
        myServo.write(servoPositions[i]);
        delay(2000);
    }
}

void setup() {
    delay(100);
    Serial.begin(115200);
    Serial.println("M&M Sorter Initializing...");

    // set LEDs to output and limit switch to input w/ pullup resistor
    pinMode(redPin, OUTPUT);
    pinMode(greenPin, OUTPUT);
    pinMode(bluePin, OUTPUT);
    pinMode(whitePin, OUTPUT);
    pinMode(limitPin, INPUT_PULLUP);

    pinMode(lightSensorPin, INPUT);

    // Stepper motor, Servo motor setup
    myStepper.setSpeed(15);
    myServo.attach(servoPin);
    myServo.write(servoPositions[1]);

#ifdef doColorSetup
    setColorReferences();
    Serial.println("Color Settings Complete!");
    Serial.println("values are:");
    for (int i = 0; i < colorCount; i++) {
        Serial.print(colors[i].name);
        Serial.print(" [red: ");
        Serial.print(colors[i].red);
        Serial.print("] [green: ");
        Serial.print(colors[i].green);
        Serial.print("] [blue: ");
        Serial.print(colors[i].blue);
        Serial.println("]");
    }
#endif
}

void loop() {
#ifdef doServoTest
    servoTest();
#else

    getColorValues();
    sort(findMatch());

    if (emptyChamberCount >= maxEmptyChamberCount) {
        showStats();
    }
#endif
}

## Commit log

2026-01-14 more options (colorSetup, servoSetup), better color detection
2026-03-01 arduino uno added
